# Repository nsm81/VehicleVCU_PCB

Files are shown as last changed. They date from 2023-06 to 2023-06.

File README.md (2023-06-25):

# VehicleVCU - 3 CANBUSs
The VehicleVCU provides three CANBUS transceivers for communication within a vehicle. An ESP32-S2FH4 microcontroller is utilised which has 4kB of flash and one CAN controller. For the other two CANBUSs, two exteral SPI CAN controllers are utilised.

## PCB & Enclosure
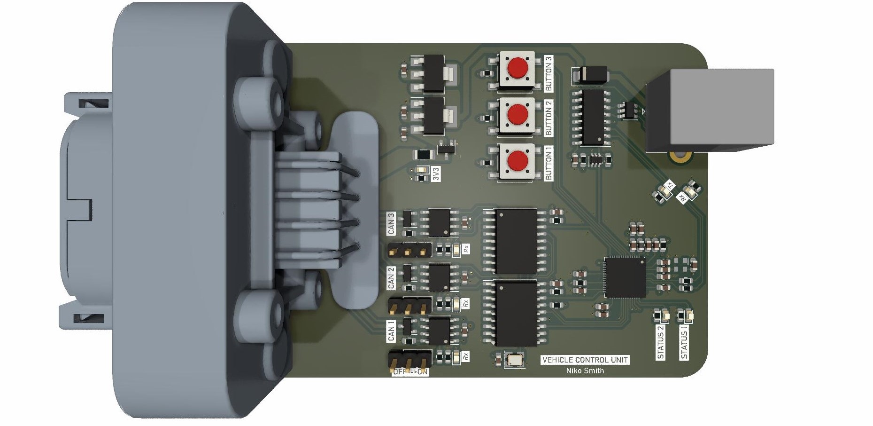
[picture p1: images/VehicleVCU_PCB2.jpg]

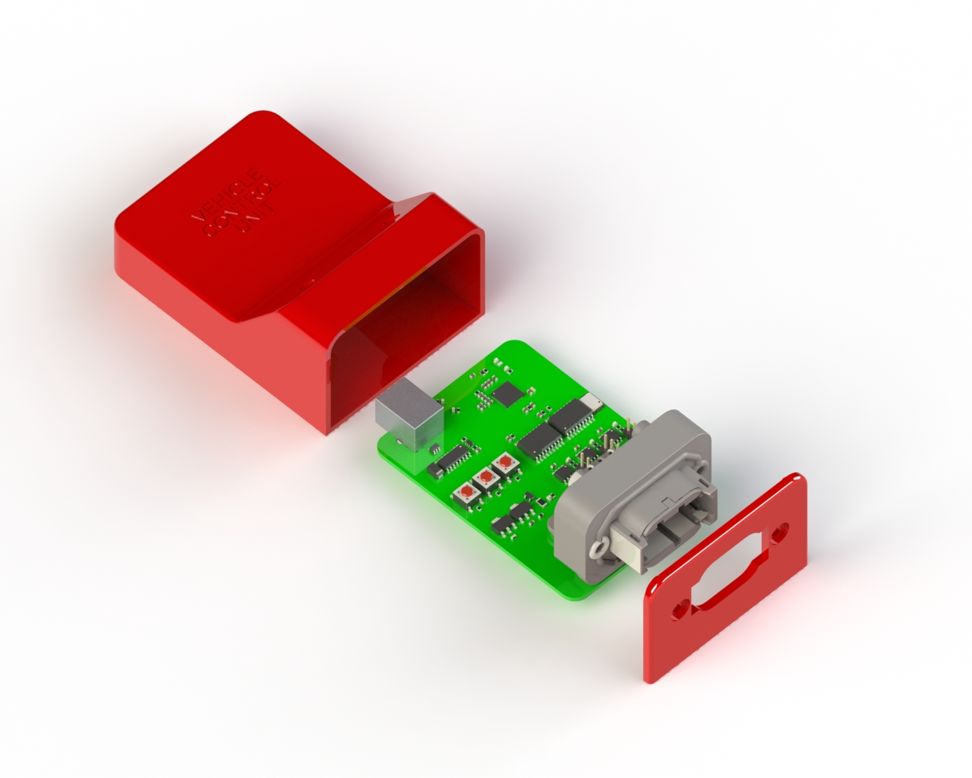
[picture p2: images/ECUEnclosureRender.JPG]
Render


## Block Diagram
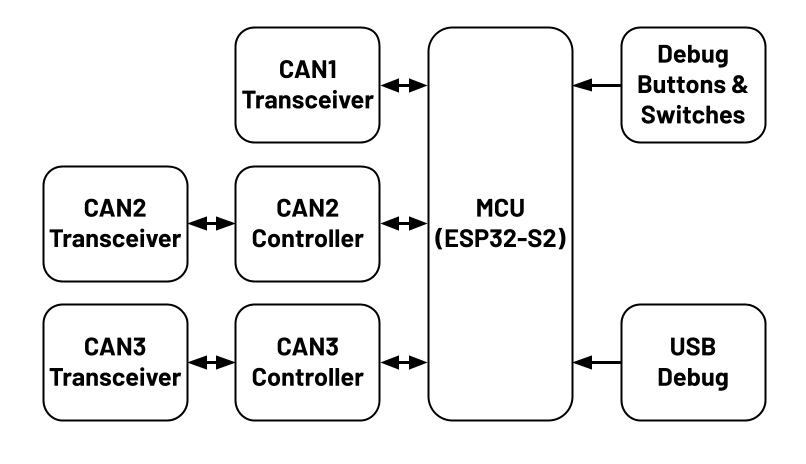
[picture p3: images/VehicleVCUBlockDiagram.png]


## MCU IO
| Description  | IO |
| --- | --- |
| Button 1 | IO4 |
| Button 2 | IO3 |
| Button 3 | IO2 |
| STATUS LED 1 | IO38 |
| STATUS LED 2 | IO37 |
| CAN1RX | IO34 |
| CAN1TX | IO35 |
| CAN1_INT | IO36 |
| CAN2_CS | IO21 |
| CAN2_SPI_INT | IO33 |
| CAN3_CS | IO9 |
| CAN3_SPI_INT | IO10 |
| MISO | IO31 |
| MOSI | IO32 |
| SCLK | IO30 |

## DTM PinOut
| Pin  | Description |
| --- | --- |
| 1 | GLV+ |
| 2 | CAN3L |
| 3 | CAN2L |
| 4 | CAN1L |
| 5 | CAN1H |
| 6 | CAN2H |
| 7 | CAN3H |
| 8 | GND |

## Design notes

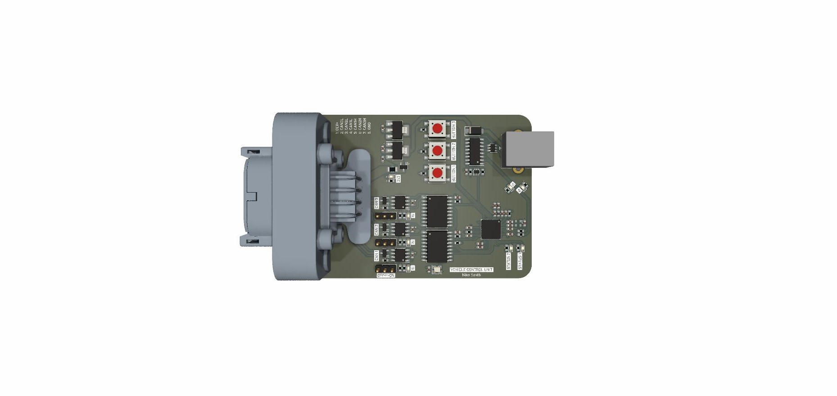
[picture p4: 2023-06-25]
images/VehicleVCU_PCB.jpg

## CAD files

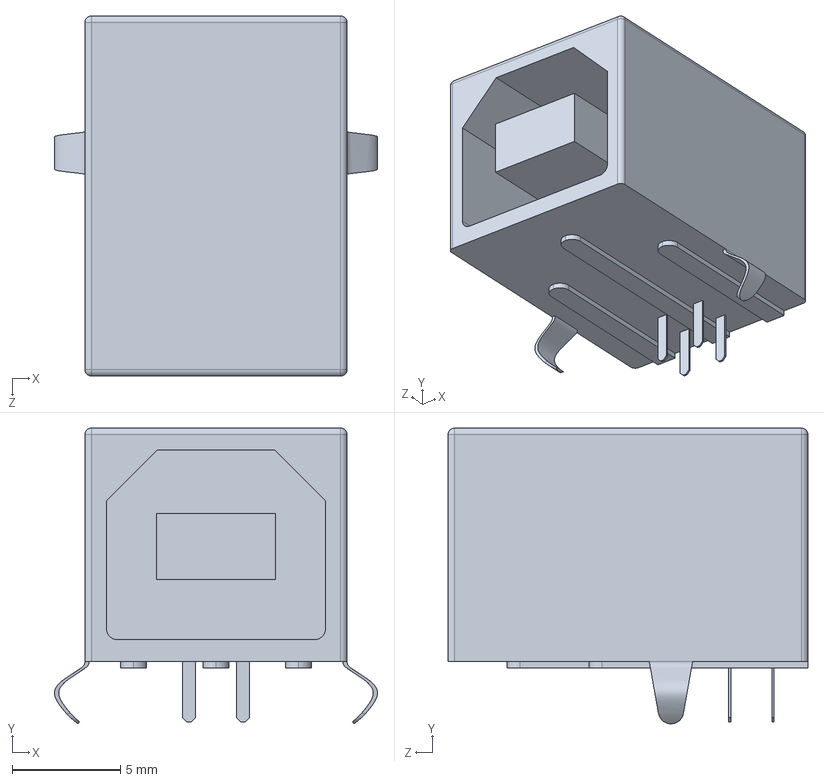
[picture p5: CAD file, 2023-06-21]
USB type-B female PCB.STEP
14.9 x 13.6 x 16.6 mm

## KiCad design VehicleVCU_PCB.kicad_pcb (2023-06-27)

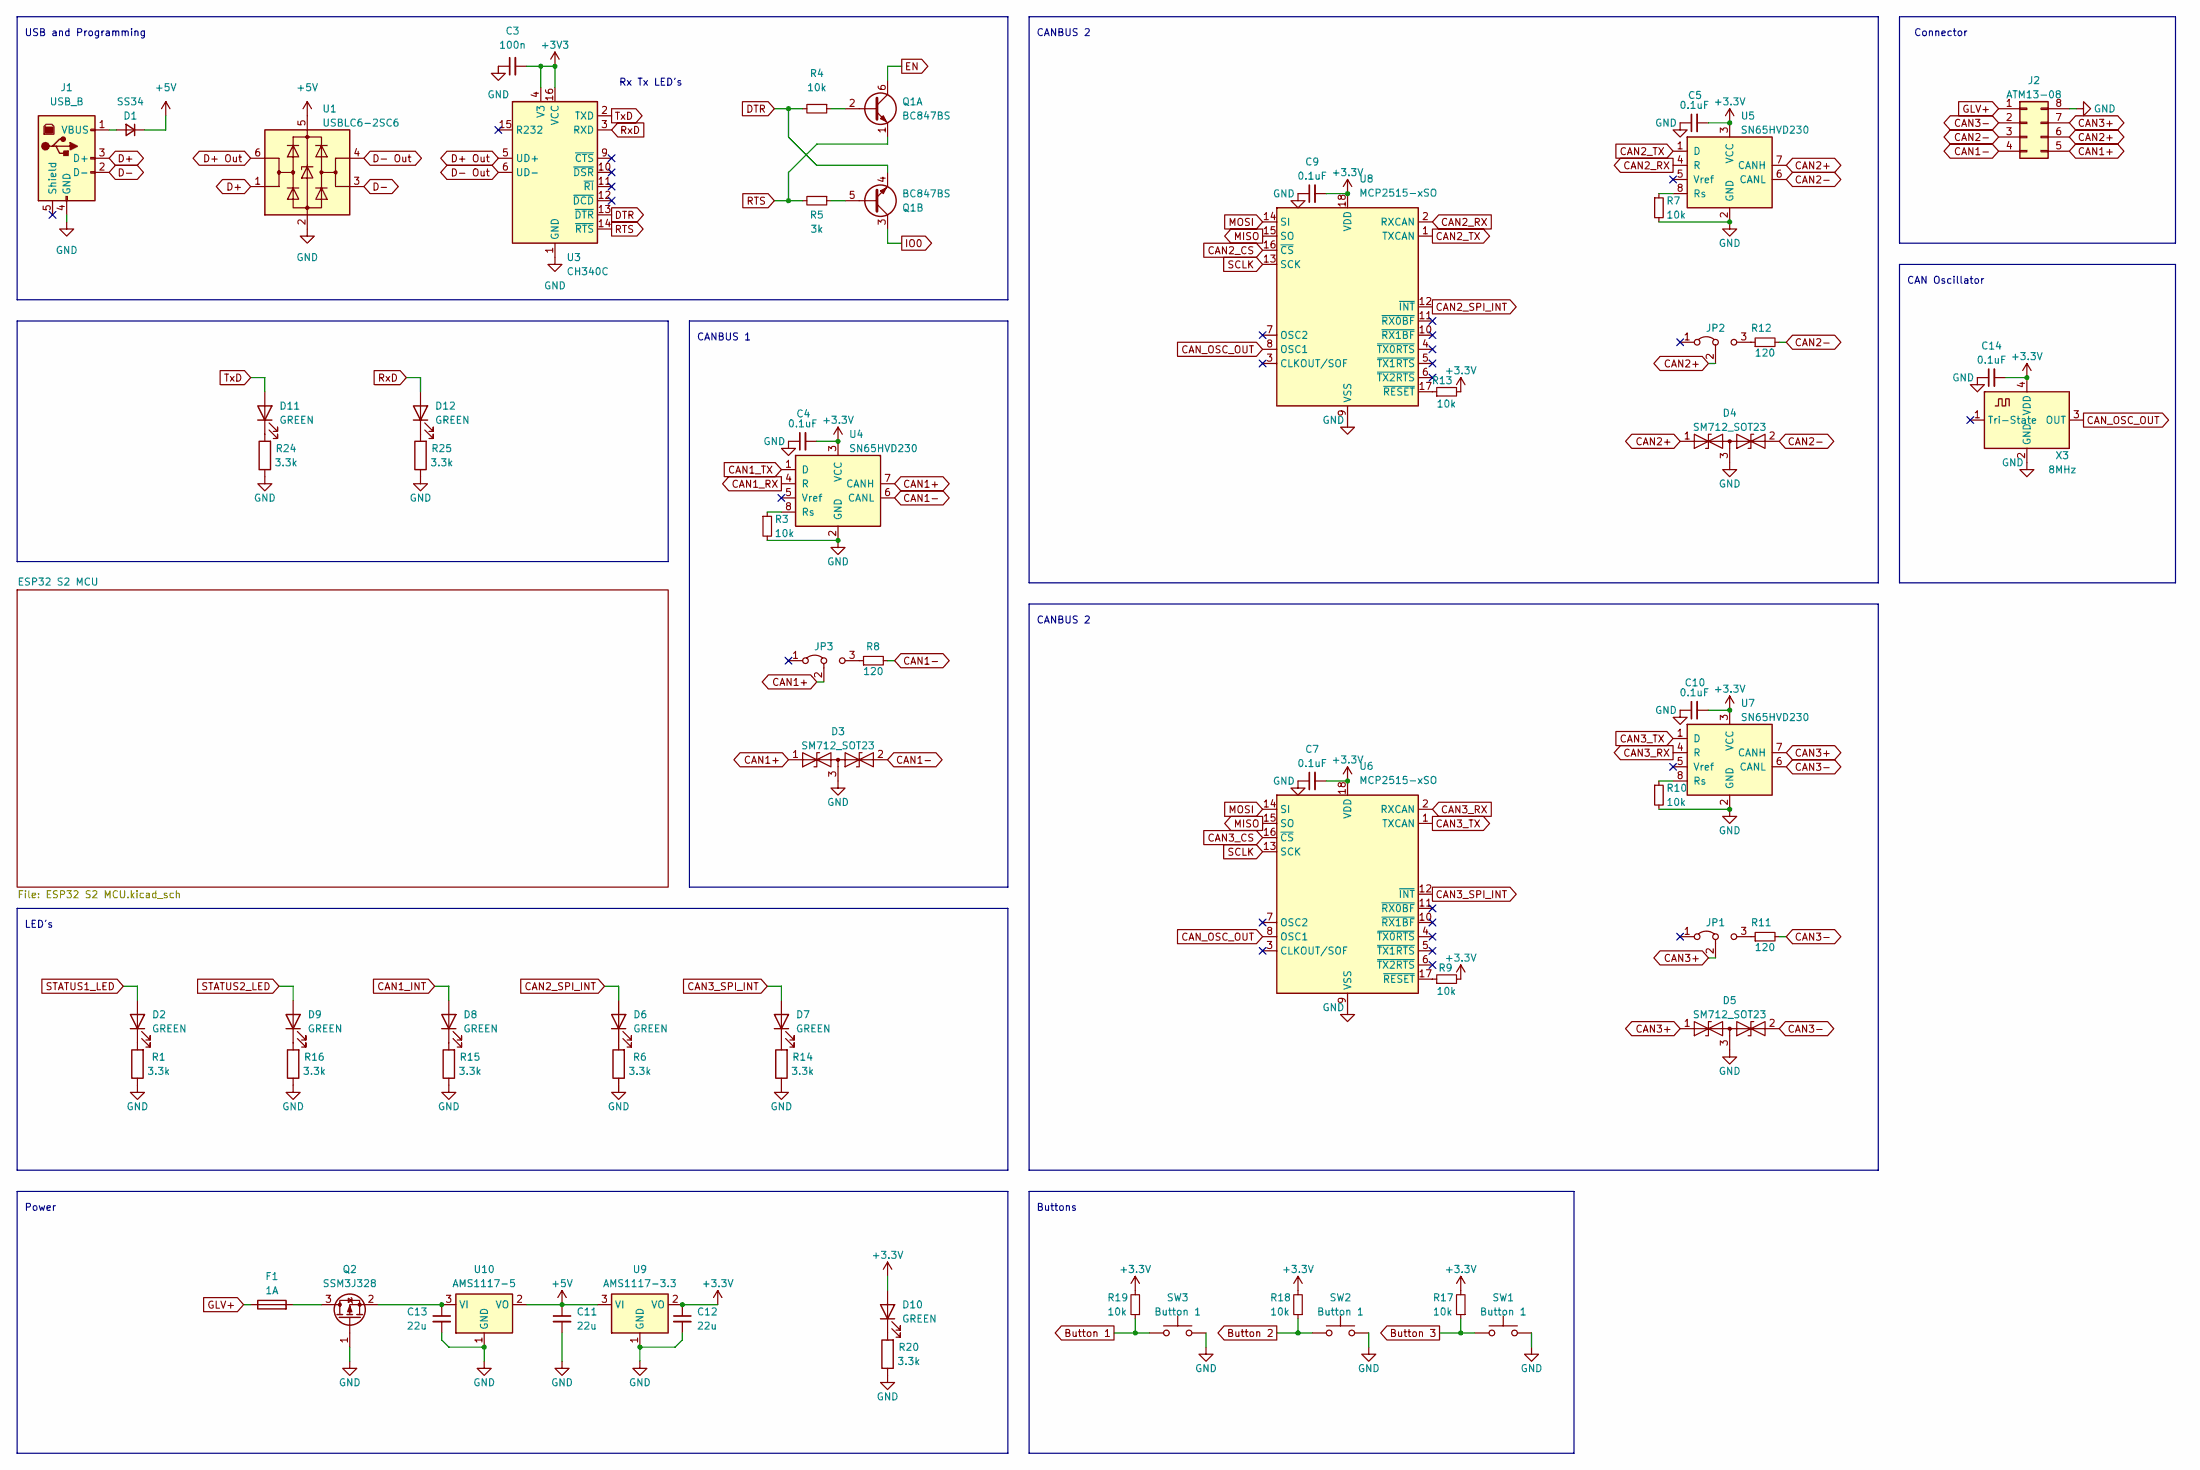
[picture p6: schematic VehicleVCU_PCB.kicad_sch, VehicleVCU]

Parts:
C3: 100n; C_0603_1608Metric
C4, C5, C7, C9, C10, C14: 0.1uF; C_0603_1608Metric
C11, C12, C13: 22u; C_0603_1608Metric
D1: SS34; D_SMA
D2, D6, D7, D8, D9, D10, D11, D12: GREEN; LED_0603_1608Metric; LCSC C72043
D3, D4, D5: SM712_SOT23; SOT-23
F1: 1A; Fuse_1206_3216Metric
J1: USB_B; USB_B_Lumberg_2411_02_Horizontal
J2: ATM13-08; ATM15-08
JP1, JP2, JP3: Jumper_2_Open; PinHeader_1x03_P2.54mm_Vertical
Q1: BC847BS; SOT-363_SC-70-6
Q2: SSM3J328; SOT-23-3
R1, R6, R14, R15, R16, R20, R24, R25: 3.3k; R_0603_1608Metric
R3, R4, R7, R9, R10, R13, R17, R18, R19: 10k; R_0603_1608Metric
R5: 3k; R_0603_1608Metric
R8, R11, R12: 120; R_0603_1608Metric
SW1, SW2, SW3: Button 1; SW_SPST_B3S-1000
U1: USBLC6-2SC6; SOT-23-6
U3: CH340C; SOIC-16_3.9x9.9mm_P1.27mm
U4, U5, U7: SN65HVD230; SOIC-8_3.9x4.9mm_P1.27mm; LCSC C12084
U6, U8: MCP2515-xSO; SOIC-18W_7.5x11.6mm_P1.27mm; LCSC C12368
U9: AMS1117-3.3; SOT-223-3_TabPin2
U10: AMS1117-5; SOT-223-3_TabPin2
X3: 8MHz; Oscillator_SMD_Abracon_ASE-4Pin_3.2x2.5mm; LCSC C717687

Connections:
+5V: C11.1, D1.1 (K), U1.5 (VBUS), U9.3 (VI), U10.2 (VO)
Button 1: R19.1, SW3.1; also elsewhere on the board
Button 2: R18.1, SW2.1; also elsewhere on the board
Button 3: R17.1, SW1.1; also elsewhere on the board
CAN1+: D3.1 (A1), J2.5, JP3.2 (C), U4.7 (CANH)
CAN1-: D3.2 (A2), J2.4, R8.2, U4.6 (CANL)
CAN1_INT: D8.2 (A); also elsewhere on the board
CAN1_RX: U4.4 (R); also elsewhere on the board
CAN1_TX: U4.1 (D); also elsewhere on the board
CAN2+: D4.1 (A1), J2.6, JP2.2 (C), U5.7 (CANH)
CAN2-: D4.2 (A2), J2.3, R12.2, U5.6 (CANL)
CAN2_CS: U8.16 (~CS); also elsewhere on the board
CAN2_RX: U5.4 (R), U8.2 (RXCAN)
CAN2_SPI_INT: D6.2 (A), U8.12 (~INT); also elsewhere on the board
CAN2_TX: U5.1 (D), U8.1 (TXCAN)
CAN3+: D5.1 (A1), J2.7, JP1.2 (C), U7.7 (CANH)
CAN3-: D5.2 (A2), J2.2, R11.2, U7.6 (CANL)
CAN3_CS: U6.16 (~CS); also elsewhere on the board
CAN3_RX: U6.2 (RXCAN), U7.4 (R)
CAN3_SPI_INT: D7.2 (A), U6.12 (~INT); also elsewhere on the board
CAN3_TX: U6.1 (TXCAN), U7.1 (D)
D+: J1.3 (D+), U1.1 (I/O1)
D+ Out: U1.6 (I/O1), U3.5 (UD+)
D-: J1.2 (D-), U1.3 (I/O2)
D- Out: U1.4 (I/O2), U3.6 (UD-)
DTR: Q1.4 (E2), R4.2, U3.13 (~DTR)
EN: Q1.6 (C1); also elsewhere on the board
GLV+: F1.1, J2.1
GND: C3.1, C4.1, C5.1, C7.1, C9.1, C10.1, C11.2, C12.2, C13.2, C14.1, D3.3 (common), D4.3 (common), D5.3 (common), J1.4 (GND), J2.8, Q2.1 (G), R1.1, R3.2, R6.1, R7.2, R10.2, R14.1, R15.1, R16.1, R20.1, R24.1, R25.1, SW1.2, SW2.2, SW3.2, U1.2 (GND), U3.1 (GND), U4.2 (GND), U5.2 (GND), U6.9 (VSS), U7.2 (GND), U8.9 (VSS), U9.1 (GND), U10.1 (GND), X3.2 (GND); also elsewhere on the board
IO0: Q1.3 (C2); also elsewhere on the board
MISO: U6.15 (SO), U8.15 (SO); also elsewhere on the board
MOSI: U6.14 (SI), U8.14 (SI); also elsewhere on the board
unnamed: D1.2 (A), J1.1 (VBUS)
unnamed: D2.1 (K), R1.2
unnamed: D6.1 (K), R6.2
unnamed: D7.1 (K), R14.2
unnamed: D8.1 (K), R15.2
unnamed: D9.1 (K), R16.2
unnamed: D10.1 (K), R20.2
unnamed: D11.1 (K), R24.2
unnamed: D12.1 (K), R25.2
unnamed: JP1.3 (B), R11.1
unnamed: JP2.3 (B), R12.1
unnamed: JP3.3 (B), R8.1
unnamed: Q1.2 (B1), R4.1
unnamed: Q1.5 (B2), R5.1
unnamed: F1.2, Q2.3 (D)
unnamed: C13.1, Q2.2 (S), U10.3 (VI)
unnamed: R3.1, U4.8 (Rs)
unnamed: R7.1, U5.8 (Rs)
unnamed: R9.1, U6.17 (~RESET)
unnamed: R10.1, U7.8 (Rs)
unnamed: R13.1, U8.17 (~RESET)
RTS: Q1.1 (E1), R5.2, U3.14 (~RTS)
RxD: D12.2 (A), U3.3 (RXD); also elsewhere on the board
SCLK: U6.13 (SCK), U8.13 (SCK); also elsewhere on the board
STATUS1_LED: D2.2 (A); also elsewhere on the board
STATUS2_LED: D9.2 (A); also elsewhere on the board
TxD: D11.2 (A), U3.2 (TXD); also elsewhere on the board

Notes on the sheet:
CAN Oscillator
Power
Connector
Buttons
Rx Tx LED's
LED's
CANBUS 2
USB and Programming
CANBUS 1

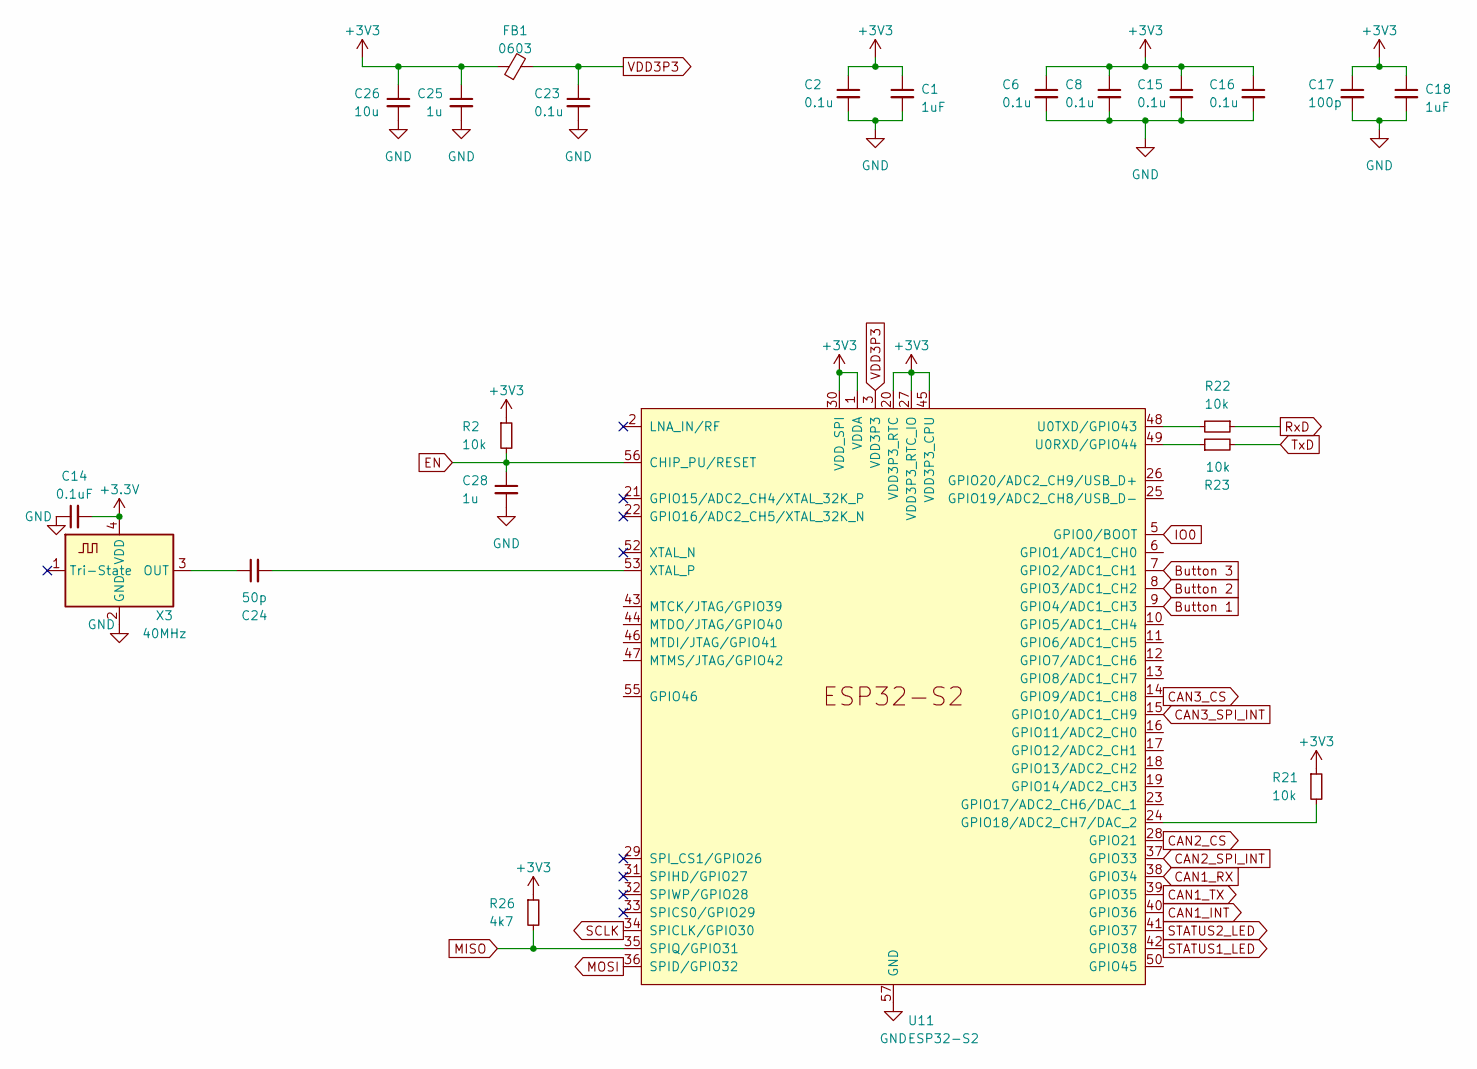
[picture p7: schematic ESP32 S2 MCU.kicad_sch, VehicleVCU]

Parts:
C1, C18: 1uF; C_0603_1608Metric
C2, C6, C8, C15, C16, C23: 0.1u; C_0603_1608Metric
C14: 0.1uF; C_0603_1608Metric
C17: 100p; C_0603_1608Metric
C24: 50p; C_0603_1608Metric
C25, C28: 1u; C_0603_1608Metric
C26: 10u; C_0603_1608Metric
FB1: 0603; L_0603_1608Metric
R2, R21, R22, R23: 10k; R_0603_1608Metric
R26: 4k7; R_0603_1608Metric
U11: ESP32-S2; QFN-56-1EP_7x7mm_P0.4mm_EP5.6x5.6mm
X3: 40MHz; Oscillator_SMD_Abracon_ASDMB-4Pin_2.5x2.0mm; LCSC C717687

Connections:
EN: C28.1, R2.2; also elsewhere on the board
GND: C1.2, C2.2, C6.2, C8.2, C14.1, C15.2, C16.2, C17.2, C18.2, C23.2, C25.2, C26.2, C28.2, X3.2 (GND); also elsewhere on the board
MISO: R26.2; also elsewhere on the board
unnamed 48: R21.2; also elsewhere on the board
unnamed 49: R23.1; also elsewhere on the board
unnamed 50: R22.2; also elsewhere on the board
unnamed 51: C24.2; also elsewhere on the board
RxD: R22.1; also elsewhere on the board
TxD: R23.2; also elsewhere on the board
VDD3P3: C23.1, FB1.2; also elsewhere on the board

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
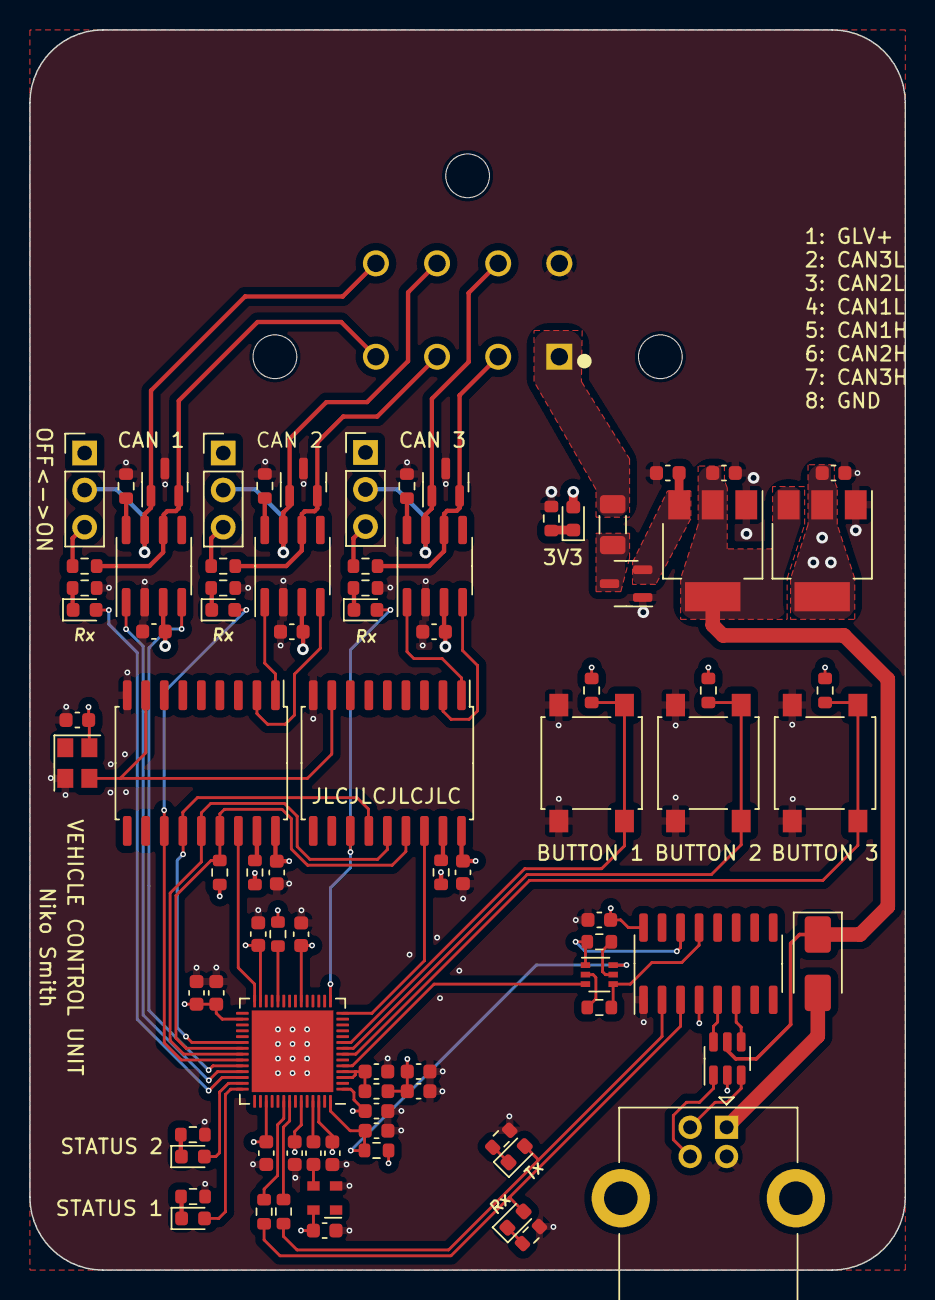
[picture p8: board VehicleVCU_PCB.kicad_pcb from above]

Board: 4 copper layers, 60.0 x 85.0 mm, 86 parts (0 on the bottom side), 67 nets.

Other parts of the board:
C27: 0.1uF; C_0603_1608Metric
U2: ESP32-S2; QFN-56-1EP_7x7mm_P0.4mm_EP5.6x5.6mm
X1: 40MHz; Oscillator_SMD_Abracon_ASDMB-4Pin_2.5x2.0mm

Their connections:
Button 1: U2.9 (GPIO4/ADC1_CH3); also elsewhere on the board
Button 2: U2.8 (GPIO3/ADC1_CH2); also elsewhere on the board
Button 3: U2.7 (GPIO2/ADC1_CH1); also elsewhere on the board
CAN1_INT: U2.40 (GPIO36); also elsewhere on the board
CAN1_RX: U2.38 (GPIO34); also elsewhere on the board
CAN1_TX: U2.39 (GPIO35); also elsewhere on the board
CAN2_CS: U2.28 (GPIO21); also elsewhere on the board
CAN2_SPI_INT: U2.37 (GPIO33); also elsewhere on the board
CAN3_CS: U2.14 (GPIO9/ADC1_CH8); also elsewhere on the board
CAN3_SPI_INT: U2.15 (GPIO10/ADC1_CH9); also elsewhere on the board
EN: U2.56 (CHIP_PU/RESET); also elsewhere on the board
GND: C27.1, U2.57 (GND), X1.2 (GND); also elsewhere on the board
IO0: U2.5 (GPIO0/BOOT); also elsewhere on the board
MISO: U2.35 (SPIQ/GPIO31); also elsewhere on the board
MOSI: U2.36 (SPID/GPIO32); also elsewhere on the board
unnamed 48: U2.24 (GPIO18/ADC2_CH7/DAC_2); also elsewhere on the board
unnamed 49: U2.49 (U0RXD/GPIO44); also elsewhere on the board
unnamed 50: U2.48 (U0TXD/GPIO43); also elsewhere on the board
unnamed 51: U2.53 (XTAL_P); also elsewhere on the board
SCLK: U2.34 (SPICLK/GPIO30); also elsewhere on the board
STATUS1_LED: U2.42 (GPIO38); also elsewhere on the board
STATUS2_LED: U2.41 (GPIO37); also elsewhere on the board
VDD3P3: U2.3 (VDD3P3), U2.4 (VDD3P3); also elsewhere on the board

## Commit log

2023-06-25 Created Production Files and Added Rendering. Just need to add silkscreen of pinout
    [ESP32 S2 MCU.kicad_sch, UCM23-PCB-ECU.kicad_pcb, UCM23-PCB-ECU.kicad_sch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]
2023-06-25 Added Pinout and Block Diagram
    [VehicleVCU_PCB-CuBottom.gbr, VehicleVCU_PCB-CuIn1.gbr, VehicleVCU_PCB-CuIn2.gbr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]
2023-06-25 Final Commit. Created ibom
    [VehicleVCU_PCB.kicad_pcb]
2023-06-27 Submitted for Manufacturing
    [VehicleVCU_PCB-CuBottom.gbr, VehicleVCU_PCB-CuIn1.gbr, VehicleVCU_PCB-CuIn2.gbr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]
